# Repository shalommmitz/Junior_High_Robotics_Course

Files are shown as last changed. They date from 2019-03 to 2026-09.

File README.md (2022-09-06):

<p align="center">
  <h3 align="center">Junior High Robotics Course</h3>

  <p align="center">
    An open-source and open-hardware course, designed to make Technology cool.
  </p>
</p>
<br>

This repository holds the materials of a robotics course that was given for more than 10 years to gifted students. The course teaches the basics of electronics, programming and robotics. The course aims to make students 'at home' with advanced, deep technologies, in hope that more of them will choose STEM as careers.
During the course, the students build a robot, which is affordable enough so they can take it home at the end of the year. This is a great motivator.

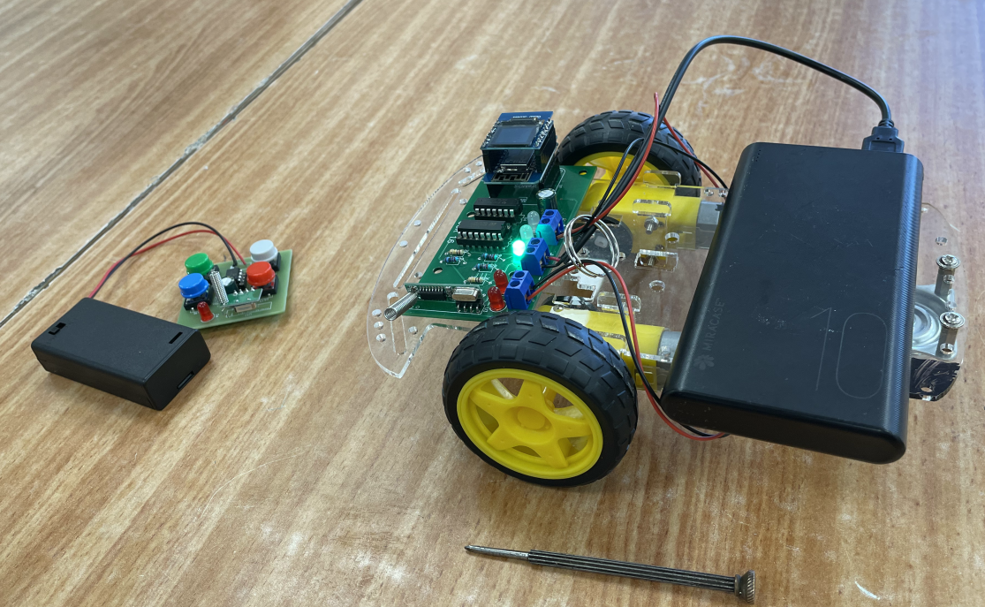
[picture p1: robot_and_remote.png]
The robot and remote-control assembled


## Table of contents

- [Course Overview](#course-overview)
- [Content of Subdirectories](#content-of-subdirectories)
- [Prerequisites and Installing](#prerequisites-and-installing)
- [Author](#author)
- [License](#license)

## Course Overview

The course was given multiple years to 7Th, 8Th and 9Th graders at the i[Ofek Gifted school](http://projects.jerusalemfoundation.org/education/education/ofek-school-for-gifted-children.aspx), located at Jerusalem, Israel.
This course teaches the following

- The basic principles of electricity (Ohm's law and related terms)
- The basic principles of electronics, including use of multi-meter
- Reading electronics schematics
- Design of PCBs
- Soldering and trouble-shooting electronic circuits
- Basic Python skills

## Content of Subdirectories

- documents_presentations:
    - [The course syllabus](documents_presentations/syllabus.md)
    - [The list of parts used in the course, including links for each item in Ali-Express](documents_presentations/22_08_Ofek_robotics_purchases.xlsx)
    - [Presentation: Motivation for the course (Hebrew)](documents_presentations/advocating_technology_at_junior_high_Hebrew.pptx)
    - [Presentation: Overview of Electronics (Hebrew)](documents_presentations/electronics_overview_Hebrew.ppt)
    - [Hands-on fun way to illustrate voltage/current/resistance and their relationship (Hebrew)](documents_presentations/ohm_law_experiment.doc)
    -[Presentation: Overview of the robot (Hebrew)](documents_presentations/robot_overview_Hebrew.ppt) 

- remoteControl_firmware
- remoteControl_hardware
- robot_firmware
- robot_hardware
- robot_PC_software

## So, you want to teach this course ?

Here is what you will need:

- One time: One item of: PIC programmer, [PIC basic pro compiler](http://store.melabs.com/prod/PBP/PBP3-2.html)
- One time: For each student: A PC or laptop,working bench, a soldering iron
- One time: For every 5 students: a multimeter, a magnifing glass, pliers, cutter 
- Every year: [kits, robots and remote parts](documents_presentations/22_08_Ofek_robotics_purchases.xlsx)

## Author

**Shalom Mitz** - [shalommmitz](https://github.com/shalommmitz)

## License

This project is licensed under the MIT License - see the [LICENSE](LICENSE ) file for details.

## Apendix A: Parts List
| Quantity per student | Quantity Ordered | Description | Order | Del | Price USD | Used by | URL | |
|---|---|---|---|-----|---|---|---|---|
| | | | | | | | | |
| First Project (Kit) | | Kits | | | | | | |
| 4 | 5 | Hour-glass leds kit | 24Aug | | 17.71 | Initial kit  | https://www.aliexpress.com/item/1005002305819829.html | |
| 4 | 5 | Alarm clock kit | 24Aug | | 26.59 | Initial kit  | https://www.aliexpress.com/item/4000302775578.html | |
| 4 | 5 | Metal detector | 24Aug | | 9.14 | Initial kit  | https://www.aliexpress.com/item/33004705384.html | |
| Parts for robot and remote | | | | | | | | |
| 15 | 8 | Wheel Chassis | 01Sep | | 68.92 | robot | https://www.aliexpress.com/item/1005004589986093.html | |
| 0 | 7 | Wheel Chassis | 04Sep | | 60.34 | robot | https://www.aliexpress.com/item/1005004589986093.html | |
| 1 | 0 | 25 PCB version 1.7 | 03Sep | | 27.51 | robot | https://jlcpcb.com/ | |
| 1 | | PCBs for Remote | | | | remote | https://jlcpcb.com/ | |
| 2 | 2 | 10 uP PIC12F675 I/P | 04Sep | | 26.7 | remote | https://www.aliexpress.com/item/4000052205464.html | |
| 1 | 0 | 1000 LED | | | | robot | https://www.aliexpress.com/item/Free-shipping-1000PCS-5-value-5mm-diffused-red-yellow-blue-green-white-R-G-B-W/2048531042.html | |
| 1 | | 100 x 40-pin stright Female | | | | robot | http://www.aliexpress.com/item/100PCS-2-54mm-40-Pin-Stright-Female-Single-Row-Pin-Header-Strip-PCB-Connector/32596334536.html | |
| 3 | 3 | 10 L239D DIP IC | 04Sep | | 7.1 | robot | https://www.aliexpress.com/item/32844099228.html | |
| 1 | 3 | 10 14pin DIP socket | 04Sep | | 7.02 | robot | https://www.aliexpress.com/item/32799921132.html | |
| 2 | 3 | 10 16pin socket | 04Sep | | 6.42 | robot | https://www.aliexpress.com/item/32800892159.html | |
| 15 | 15 | Wemos D1 Mini V3.0.0 | 05Sep | | 32.55 | robot | https://www.aliexpress.com/item/1005001621896145.html | |
| 12 | 15 | Oled Display 64x48 | 05Sep | | 27.75 | robot | https://www.aliexpress.com/item/1005001621659840.htmlhttps://www.aliexpress.co/item/Free-Shipping-0-66-inch-Wemos-Oled-64X48-IIC-I2C-LCD-OLED-LED-Dispaly-Shield-for/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 | |
| 2 | 2 | 20 8pin socket | 05Sep | | 4.02 | remote | https://www.aliexpress.com/item/32878848553.html | |
| 0 | 0 | 100 x 1000u cap | | | | remote+robot | http://www.aliexpress.com/item/Free-Shipping-DIP-Electrolytic-capacitor-1000UF-16V-8-12mm-100pcs-lot-NEW-in-stock-if-can/2010462041.html | |
| 5 | 0 | 500pcs 220 ohm resistors | | | 8.37 | remote+robot | https://www.aliexpress.com/item/32829082640.html | Note: 5 per robot, 1 per remote |
| 2 | 0 | 200pcs 100K ohm | | | 3.31 | robot | https://www.aliexpress.com/item/1005002000626397.html | Note: 2 per robot |
| 12 | 25 | RF TX RX + ANT | 05Sep | | 21.29 | remote+robot | https://www.aliexpress.com/item/32980820915.html | |
| 3 | 7 | 25pcs push btn | 05Sep | | 7.25 | for remote | https://www.aliexpress.com/item/32834276752.html | |
| 0 | 0 | 10 2 AA Battery Holder | | | 6.99 | for remote | http://www.aliexpress.com/item/10PCS-2-AA-3A-Battery-3V-Holder-Box-Case-with-5-5-Leads-and-ON-OFF/1985883563.html | |
| 1 | 2 | 20 pcs SN74HC04N IC | 05Sep | | 8.06 | for remote | https://www.aliexpress.com/item/1005002920656915.html | |
| 4 | 13 | 10 pcs terminal block | 05Sep | | 24.12 | remote+robot | https://www.aliexpress.com/item/4000899450689.html | |
| 12 | 7 | power bank | 05Sep | | 63.7 | for robot | https://www.aliexpress.com/item/1005004701731413.html | |
| | 7 | power bank | | | 63.7 | for robot | https://www.aliexpress.com/item/1005004701731413.html | |
| 12 | 6 | USB power cable | 05Sep | | 4.32 | robot | https://www.aliexpress.com/item/4001022946203.html | |
| | 6 | USB power cable | | | 5.32 | | https://www.aliexpress.com/item/4001022946203.html | |
| | 6 | USB power cable | | | 6.32 | | https://www.aliexpress.com/item/4001022946203.html | |
| | | TOTAL USD | | | 532.88 | | | |

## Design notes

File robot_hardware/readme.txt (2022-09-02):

The files in this folder describe the robot hardware.
You might use the free version of the software 'diptrace' to view or modify those files.
There are two versions of the schematics as .PNG: white (optimized for viewing) and black (optimized for printing)
The .zip file contains the production files, used to manufacture the PCBs.
I had good experience with jlcpcb.com.

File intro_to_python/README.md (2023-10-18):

## An introduction to Python

Lesson 1: 

  - Teach the 3 basic data types (num, string, bool), print. 
  - Exercise w/online-python.com: print values, print multiple values

Lesson 2: 

  - Teach list (the first non-basic data type)
  - Concept: subordinate lines
  - Teach loop
  - Exercise: print (unformatted) mult table

Lesson 3: 
     
  - Introduce replit.com. 
  - Demo: run `draw_a_point.py` in replit
  - Exercise: draw a line (using loop)

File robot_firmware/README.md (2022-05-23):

Shalom Mitz			17th May 2022

# OVERVIEW

The procedure below shows how to program the robot 'brain'.

The brain is the 'WEMOS D1 Mini' part, which is based on the ESP8266 processor.
The brain can be programmed with or without the display-module connected.

# Steps:

1. Install software:

   1.1. On Windows: 
       
        - Install Python: Download and install the latest version from https://python.org 
        
           IMPORTANT: Turn on "Add Python to Path" at first screen of installation
        - Install the drivers for the WeMOS serial drivers

   1.2. Install the sw to burn the 'robot brain' (=ESP8620):   `pip install esptool`
   1.3. Install the sw  that will transfer files to the robot brain: 'pip install adafruit-ampy`
   
2. Connect the robot-brain to a PC, using a normal 'Android' micro-USB cable

Note: 
   Normally we program the brain with the firmware-image file present in this directory.
   However, you can also use the generic microPython image, present at http://micropython.org/download#esp8266

3. Program the brain with the microPython image: 
   - ON LINUX: 

       Run './initial_firmware_loading_for_linux'

   - ON WINDOWS:

       Run 'initial_firmware_loading_for_windows'

4. Find the serial port used by the robot-brain:
  
   The easiest way is to look at the messages when running esptool (previous step).
   
   If this does not work:
  
   ON LINUX:
   
   Using terminal, run 'ls /dev/ttyUSB*'. This should show /dev/ttyUSB0
   If only /dev/ttyUSB2 exists, you should edit the file 'initial_firmware_loading_for_linux' to reflect this.
   If the 'ls' command above does not show anything, the D1 was not recognized.
   This must be resolved before continuing.

   ON WINDOWS:
   
      Normally, "COM4" is used on Windows
      To see the actual port:
         - Open the "Device Manager":
             - Right-click on "Computer" or "This PC" icon
             - At the menu that will open, choose "Manage"
             - choose "Device Manager"
         - Expand "LPT and COM ports"
         - Notice the existing serial ports (called "COM" and a digit)
         - Plug-in the robot brain to the PC, using a USB cable
         - Notice the name of the new COM port. This is normally "COM4"

5. Burn the additional files:
   Run:

     - On Windows: `send_all_files_windows.cmd`
     - On Linux:   `./send_all_files_linux`

   You can run the command "import verifyFiles" to verify that the files were correctly loaded.

6. Sanity check: disconnect the D1 from the USB and plug back.
   When you re-connect the D1, one of the LEDs should blink twice.
   If the LED does not blink, or blink all the time, try to run 'burn' again
   Note: Detailed instructions of programming the D1 and troubleshooting can be found at:
   http://docs.micropython.org/en/latest/esp8266/esp8266/tutorial/intro.html#deploying-the-firmware

# Testing:

1. Connect to the brain: 
   Once connected, the brain looks like serial port at /dev/ttyUSB0 (rarely: /dev/ttyUSB1) on Linux or CAM4 on Windows.

   You can connect to it using: putty, minicom, screen, or any other 'terminal emulation' software
   Here are detailed instructions using Putty:

   - Open putty
   - Define a serial session: 
      - Choose "Serial" as the connection type     
      - Set the port (Normally: COM4 or /dev/ttyUSB0)
      - Set the speed: 115200
   - Open the connection: Click on "Open"
   - Press "Enter": you should see the Python prompt (>>>)
     Do not continue to the next steps before you get the prompt !
     You can try to close Putty, disconnect the brain, reconnect the brain and launch putty again.
     You can also try to burn the image again.

   Once you are connected, hit "Enter" few times, and you should get the ">>>" REPL prompt.
   If you do not get the prompt, try unplug/plugin from USB. If this fails, try 'burn' again.
   There is no point to continue w/o the REPL prompt.

   Also, once you are connected, you can type the command "import demo".
   This should send few strings to the console and then display some pictures on the attached display. 

Steps that are repeated each time the D1 is used:

1. Connect to the PC/laptop to the WiFi access-point created by the D1:

   Look at the available WiFi networks for a network called "MicroPython-xxxxxx" (the 'xxxxxx' part is different for each D1)
   Connect to this network.
   Note: This will probably disconnect you from the Internet. 

2. Connect to the robot using WebREPL:

   If needed, download the webrepl files from  https://github.com/micropython/webrepl.
   Open the file "open webrepl.html in a browser. 
   You should get a prompt to choose password (first time) or login.
   After login, you should get the ">>>" prompt. You are also able to upload and download files.
   There are more details at: https://github.com/micropython/webrepl

3.  Using WebREPL, import the 'robot' module:
    
    Once you get the ">>>" prompt,  enter the command `import robot`
    This will define 4 outputs:
    pwmRight, dirRight, pwmLeft, dirLeft
    Each of those can be set to high or low, for example:
    pwmRight.low() or pwmLeft.high() 
    Experiment: those 4 pins control the motors.

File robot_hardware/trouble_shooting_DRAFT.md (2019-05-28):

My robot does not move
----------------------
Those are the possible causes:

1. No power
2. 'Brain' not fully functional
3. Motors not connected
4. Issue with the H-Bridge IC (U2, L293D)

Procedure to Fix:

1. Verify that power is Ok
   The center LED should be on. If not, you have no power.
   If the LED is on, use multimeter (at V-DC-20V position) to measuer the input voltage. It should be atleast 4.8V. If less, you probably have to change the battries.
   If there is no voltage, start measuring voltage from the battries, until you find where is the disconnect.

2. Verify brain works Ok
   We proceed to this state assuming we verified that power is Ok.
   The easiest way to verify that the brain is fully functional is to switch termorarirly to brain from a known-to-be-working robot. If another, known-to-work, brain is not available, the best way is to continue the procedure, while watching carfully the performance of the brain. Another possiblity is to reflash the brain (rarly needed) and reload all the files.

NEED TO ADD LINK TO FLASHING THE FILES

3.  Verify that the motors are connected
   This one is easy: Using your hand, turn one wheel both ways. One of the two LEDs associated with each whell should light momentarily. Repeate for the other wheel. Fix any issue found.

4. Verify the correct operation of the H-bridge.  
   Issues with the H-bridge are the most common reason why robot won't move.
   Here are the steps to debug this IC:
   4.1. Open the schematics and zoom on U2. The schematic is at NEED TO ADD LINK TO SCHEMA
   4.2  Get a multimeter, and set it to measure Volts-DC-20V. Connect the "-"/black probe to one of the ground point of the robot, for example at the battries "-" terminal.
   4.3 Look at the schema. The H-bridge IC has two connections to the power-supply. Check that both of those connections are connected to the 5V or so comming from the battries.
   4.4 Verify connection from the brain to the pwmLeft and pwmRight points
       NEED TO ADD CODE
       NEED  TO ADD LINK TO PROCEDURE TO GET REPL (Python prompt).

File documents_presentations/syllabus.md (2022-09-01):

# Syllabus

## Background

This course evolved during the 11 years I have been teaching at the Ofek school for gifted children, in Jerusalem Israel.

It is composed of two courses: Basic course and Advanced course.
Both courses are for a full academic year, once weekly, each session is two academic hours.
In a typical year, this means 26 sessions.

The kids are mostly 7th or 8th grades.

## Curriculum Highlights for basic course

1. Basic theory and practice of electronics
   In parallel: build a small kit: mainly to put the theory in context and to practice soldering
2. Design the PCB for the remote control
3. Start building the robot
4. Build the remote control
5. Finish building the robot
6. Test/troubleshoot
7. If time allows: Study a bit of Python and program the robot

## Curriculum Highlights for the advanced course

1. Review/study Python
2. Make sure robot work, fix as needed
3. Lake: a fun exercise to develop Python skills
4. Basic machine vision
5. Controlling the robot using Python
6. Tie everything together: Use machine vision to control the robot
7. As time allows: basic neural network in Python

## Detailed Basic Course Syllabus

Note: The numbers are the week

 1. Teach: Electricity basic theory: 
    - Ohm law, resistors, basic circuit calculations
    - Review: electrical charge, current, voltage (charge=current*time)
    - Fun optional project: take bottles, fill w/water, simulate resistance

        - Prepare corks w/one, two or three holes
        - Mark 3 levels on the bottles
        - Ask kids to measure water drip out of the bottles (into one-time cups) on each cork/water level permutation
        - Ask them to draw the relationship and deduct Ohm's law

  2. Teach: Electronics hands-on basics: 

        - Use of multi-meter
        - Soldering: How-to + Review safety points: danger of fire, damage to eyes, burns, mark tables
        - Identifying components

     Hands-on:

        - Solder wire (each 5 cm or so) into shapes, such as rectangular or triangle

  3-5. Hands-on: First build project: Various kits
       Present to the kids examples of electronic-schematics
       Some effort to debug the kits - not insist on all kits working

  6-8. Teach:

       - Basics of Radio-frequency: what is RF, Uses to send data, modulation, Antenna
       - PCB: Alternatives (wires, wire-wrap), what it is, one side/two sides/multiple layers
       - Remote control basic-principles and schematics
       - Show installation and basic usage of DipTrace sw

       Hands-on:
       - Draw schematics for the remote using diptrace
       - design PCB for RF remote using diptrace

  10. Teach:

      - Presentation: the robot components
      - Integrated Circuits: Tube to Transistor to IC. Examples uses + packages

      Hands-on: build robot chassis, tests w/just motors and batteries

  11. Teach: Robot schematics
      Hands-on: continue build chassis
  12-15. Hands-on: Build Robot main board
  16. Hands-on: Debug robot
  17-18. Build remote control (dependant on PCB arriving)

  If time allows:

    - Fun: robot competitions, using the remotes
    - Control the robot from phone or PC using WiFi
    - Customize the picture displayed by the robot-display

A Real Basic Course (partial Corona - atypical):

 - Lesson #1 (12Oct2021): Basic soldering
 - Lesson #2 (19Oct2021): ?
 - Lesson #3 (16Nov2021): Assembling robots
 - Lesson #4 (23Nov2021): Assembling robots
 - Lesson #5 (07Dec2021): Finishing of robot chassis assembly + into to designing the remote PCB
 - Lesson #6 (14Dec2021): Remote PCB intro and start design
 - Lesson #7 (21Dec2021): Continue remote-control PCB design
 - Lesson #8 (28Dec2021): Continue design the remote PCB
 - Lesson #9 (04Jan2022): Finish remote PCB design and introduce robot schematic
 - Lesson #10 (11Jan2021): Finish previous tasks + explain robot schematics + start build rob
 - Lesson #11 (18Jan2021): Review robot schematics, tube-->transistor-->IC, cont build robot elect
 - Lesson #12 (01Feb2021): Review robot schematics + assemble robot pcb
 - Lesson #13 (08Feb2021): Hands-on intro to Python (vars, for, if)
 - Lesson #14 (22Feb2021): Build the remote control
 - Lesson #15 (22Mar2021): Continue assembling the remote control PCB
 - Lesson #16 (29Mar2021): Continue remote-control assembly
 - Lesson #17 (05Apr2021): Remote: assemble PCB + test + burn uPs
 - Lesson #18 (26Apr2021): Continue remote-assembly: continue burn chips
 - Lesson #19 (03May2021): Burn firmware to robot
 - Lesson #20 (10May2021): Burn sw to the robot brain

## Advanced Course (Work in Progress):

   1-3. Study Python:
        Either frontal intro w/exercises OR self study at CodeAcademy

   4. Teach: intro to network protocols, bits, bytes, hex. The robot protocol

      Exercise: Divide class to groups and challenge them to decode and parse messages:
          The messages will contain specs for food to server at restaurant
          One group will create the messages and the other group will draw the 'plates'
          
          Decrypt the "lake" protocol ???
          
   5. Personal project

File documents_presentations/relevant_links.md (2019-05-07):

How to read schematics: https://learn.sparkfun.com/tutorials/how-to-read-a-schematic

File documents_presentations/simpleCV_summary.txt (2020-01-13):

from SimpleCV import *

# create image object by reading file
img = Image("old/donkey.jpg")

#show image object and wait for user to press ENTER
img.show()
raw_input(">")

#save image
#img.save("fn")

#clone the imgage
clone = img.copy()

#create smaller copy of the image
thumb = img.scale(90,90)

#cut part of the image
cropped = img.crop(100, 100, 50, 50)

#find corners
corners = img.findCorners()

#find blobs of color
blobs = img.findBlobs()
print blobs
blobs.draw()
img.show()
raw_input(">")
##blobs are returned in order of area, smallest first
#print "largest green blob at " + str(green_blobs[-1].x) + ", " + str( green_blobs[-1].y)

bigface = face.scale(3)

rotated = lenna.rotate(90)

#split image into channels and unite again
(r,g,b)=img.splitChannels()
#new = img.mergeChannels(None,b,g)
new = img.mergeChannels(r,b,g)

#convert image to grey
img.toGray()

matrix = grey.getNumpy()
print matrix[0][0]

yellow_car = car.colorDistance(Color.YELLOW)
only_car = car - yellow_car
only_car.meanColor()
source.findTemplate(template,threshold=t,method=m)

img1.sideBySide(img2).show() #show sidebyside

img.dl().circle((10,10), 10, Color.RED) #draw circle

#get blobs
screensize = img.width * img.height
min_blob_size = 0.10 * screensize # the minimum blob is at least 10% of screen
max_blob_size = 0.80 * screensize # the maximum blob is at most 80% of screen
blobs = img.findBlobs(minsize=min_blob_size, maxsize=max_blob_size) # get the largest blob on the screen

#get width and height of image
    width = img.width;  height = img.height

#get distance from specified RGP color
imgDiffFromBlue = img.colorDistance( (21, 28, 63) )   #R, G, B

#Find edges of image
img = img.edges()

# find lines in image
lines = img.findLines()
#find longest line
longest_line = lines.sortLength()[0]

#find match of small pic in big pic
t = 5
#methods = ["SQR_DIFF","SQR_DIFF_NORM","CCOEFF","CCOEFF_NORM","CCORR","CCORR_NORM"] # the various types of template matching
m = "CCOEFF"
result = source
dl = DrawingLayer((source.width,source.height))
fs = source.findTemplate(template,threshold=t,method=m)
for match in fs:
    if match.y<38: continue #upper end of the pics is legit logos, matches not relevant
    dl.rectangle((match.x,match.y),(match.width(),match.height()),color=Color.RED)

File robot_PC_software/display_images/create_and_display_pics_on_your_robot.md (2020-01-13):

#How to create an image and display it on the robot's display

## Prerequisits:

Make sure all needed software is installed on your PC, as detailed at the files "install_needed_software_linux.txt" and "install_needed_software_windows.txt"
      During the installation, enable the check-box "Add Python 3.7 to Path"

Make sure the firmware and related files are loaded into the robot-brain. 
This is needed to be done only once on a new robot-brain.
The needed procedure is detailed at the folder 'robot_firmware'
  
## Create a new image that have the following attributes:

     size:  64 x 48   (This is the size of the display)
	 Color depth: black & white
   Or, you can start with one of the pre-existing images (.bmp) in this directory.
 
## Edit the image

You can edit the image with any image editing tool, such as mspaint, gimp, paint.net or pinta.

## Save the image, specifing the 'bitmap' format.

   It is important to keep the correct size and color depth

## Create the .hexImage file:

   The .hexImage file can be used by the robot software.
   
   Run:
   
        python convert_bmp_to_hex_Image.py <file_name.bmp>
        
   This will create a .hexImage file

## Preview the .hexImage file:

   run: 
   
        python show_hexImage_on_pc.py <file_name.hexImage>.

   If you don't like what you see, you can edit/save/convert/preview until happy :-)

## Upload the .hexImage file to the robot:

   -  Find which COM port the robot-brain is using:
      ON LINUX: the name is normally /dev/ttyUSB0 (or sometimes /dev/ttyUSB1)
      ON WINDOWS:
      Open the "Device Manager":
         - Right-click on "Computer"
         - choose "Manage"
         - Expand "LPT and COM ports"
         - Notice the existing serial ports (called "COM" and a digit)
         - Plug-in the robot brain to the PC, using USB cable
         - Notice the name the new COM port. This is normally "COM4"

   Loading the file might be done using ampy or webrepl

   Using ampy:   
   
       Linx:  ampy -p /dev/ttyUSB0 put <file name>
   
       Windws:  ampy -p com4 put <file name>
   
   Details on ampy: https://learn.adafruit.com/micropython-basics-load-files-and-run-code/install-ampy
   
   Details on webrepl: https://github.com/micropython/webrepl

## Displaying the image on the robot:

Connect to the robot and get the REPL prompt.  
Connecting to the robot can be done:

- Using WiFi: 

    Download from github the repository "webrepl.
    
    The robot 'publish' a WiFi network, called 'born' by default.
    Connect to this network.

    Now, open the .html page in the 'webrepl' repository, by double-clicking on the file.

- OR, using a USB cable:

    Connect the robot to a PC using a standard 'Android' usb cable
    Run any 'serial terminal' program, such as putty or minicom.

    On Windows, use Putty: 
      - Select "serial" as the connection type
      - Open the Serial-ports parameters window: At the left-side "Category" tree, choose the bottom entry, which is "Serial"
      - Set "COM4" as the port
      - Set "115200" as the speed.
      - Choose "Flow control" to "None"

    On Linux, use minicom:
    - Disable hardware-flow-control
    - use "/dev/ttyUSB0" as the port 
    - Specify "115200" as the speed.

    When you are correctly connected to the robot, you should get the ">>>" prompt.
    You might need to press the "Reset" button

- Displaying the image
    Run the following:
   
       >>> import display_hexImage as d
       >>> d.display_image("abc.hexImage")

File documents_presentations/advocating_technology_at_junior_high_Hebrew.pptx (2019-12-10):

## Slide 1

שיווק הי-טק בחטיבה

שלום מיץ מאי 2019

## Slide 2

תוכנית

- התנסות
- מי אני
- למה
- עשיה
- יתרונות
- חסרונות
- התנסות

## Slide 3

התנסות

- לימוד בינרי והקס
- או סרט של רובטים רוקדים ?

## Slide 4

מי אני

- מהנדס אלקטרוניקה ומחשבים
- Technical Leader at Cisco Now at Synamedia
- מלמד פעם בשבוע ב 11 השנים האחרונות
- מורעל טכנולוגיה ומחשבים

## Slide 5

למה

- להרעיל את התלמידים לטכנולוגיה
- חשיפה לאיך הי-טק עובד
  - טעימה של איך פיתוח טכנולוגיה עובד
- נצחונות בהתמודדות אם אתגרים אמיתים
- הטפה לרעיונות ה- Open Source כולל הטפה ל- Linux
- לקרב בנות ל- STEM

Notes: What is unique/interesting in Hi-tech:
Answers not known ahead of time
Agenda not well defined - “somehow” reach goal
No authoritative source of knowladge
Up=to-date technology used
Course changes every year
Real-world tools used
Everything done for the first time (sort of)
Lot and lots of English...

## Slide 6

עשיה

- שעה וחצי, פעם בשבוע, כיתות ז עד י
- קורס בסיסי: אלקטרוניקה ובנית רובוט
- קורס מתקדם: תכנות הרובוט וראית מכונה
- סביבה “חצי אפויה” -- כמו בחיים
- בסוף הקורס: רובוט לקחת הביתה
- חומרי הקורס ב- github
- junior_high_robotics_course

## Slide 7

עשיה: השיעור

- מבנה השיעור:
  - 10%: הצגת המטרה והסבר קצר
  - 90%: עבודה עצמית – המורה כ- enabler
- שימוש בכלים “מהעולם האמיתי”
- עידוד פרויקטים עצמיים
- המורה לא כל יודע
- עידוד עזרה הדדית, ואחריות

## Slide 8

יתרונות

- התלמידים נהנים
- המורה נהנה
- יותר תלמידים ילמדו ויעבדו בהי-טק ???
- אורינות טכנולוגית משופרת ?
- קרוב בנות ל- STEM ?
- לימוד וחקר כהנאה - חוויה מתקנת ?
- מקום לשונות

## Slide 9

חסרונות

- לא כולם מבינים (כולל המורה)
  - כמו בעולם האמיתי
- מעבר על פני השטח
- לא כולם מצליחים
- דורשני ולא סלחני לחיסורים

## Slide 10

סוף והתחלה

- התלמידים מסתכלים על הדפסות התוכנה של הרובוט
- תלמיד א: איך מתי מתאים שאשתלט על המחשב שלך ונפעיל את המצלמה ? לשנות את זה ?
- תלמיד ב: אני לא יודע. בא נסתכל על הקוד.

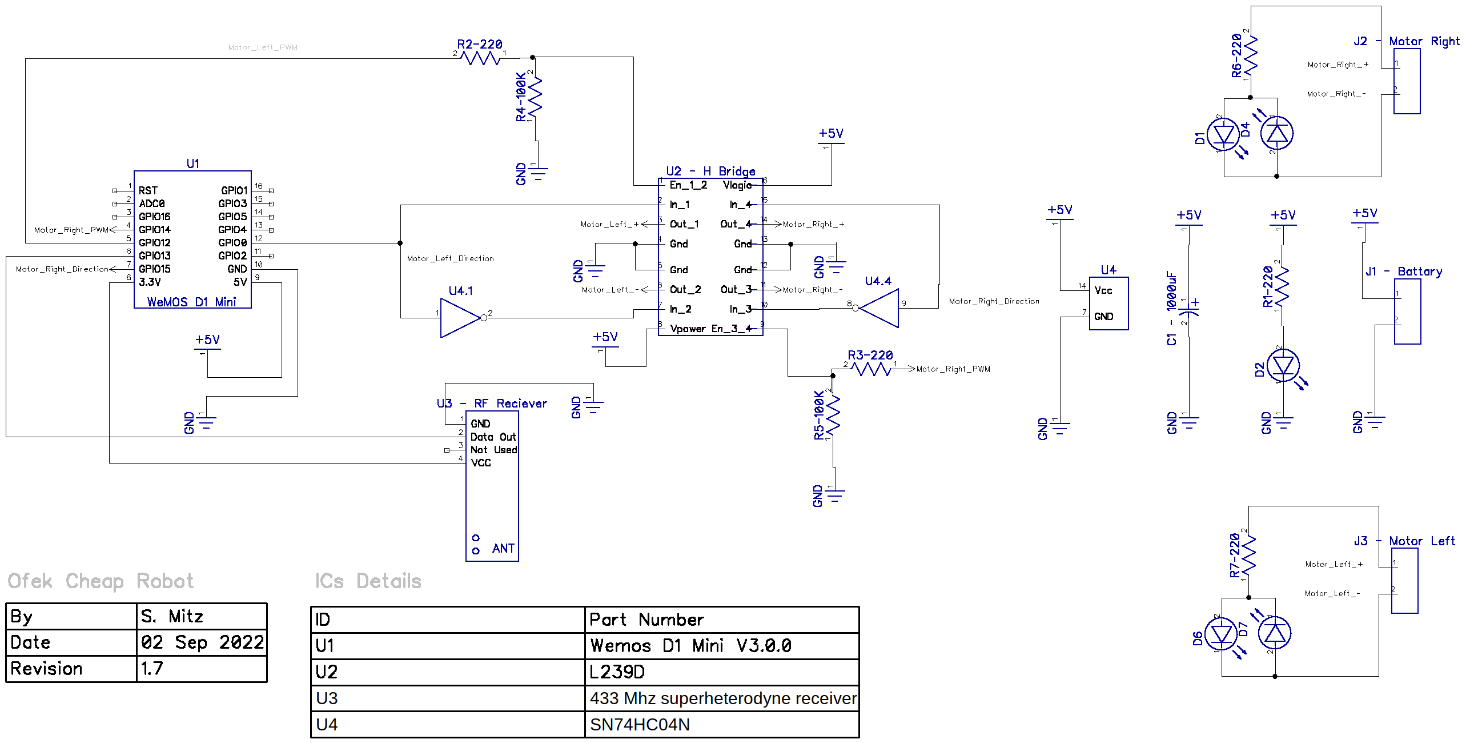
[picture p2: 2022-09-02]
robot_hardware/robot_v17_scematics_white.png

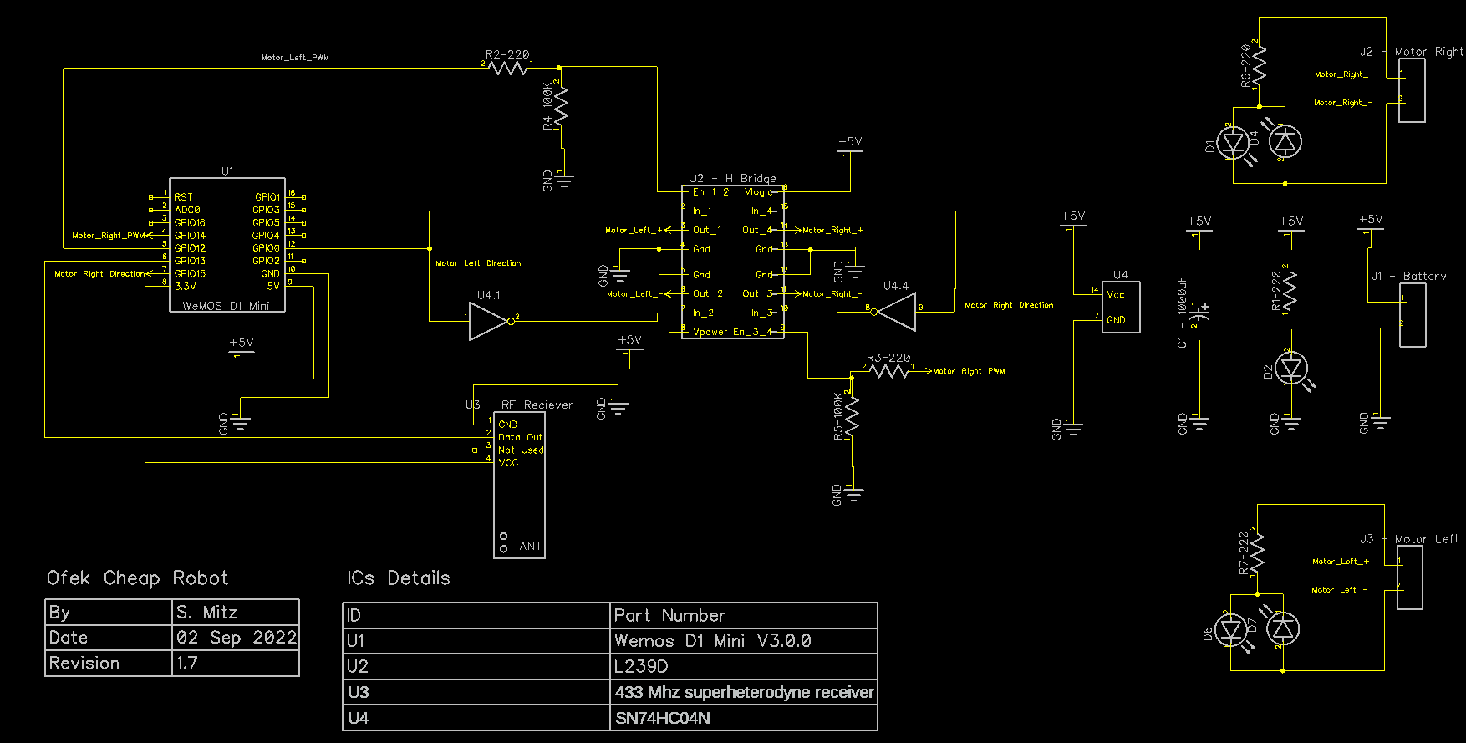
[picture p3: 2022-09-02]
robot_hardware/robot_v17_scematics_black.png

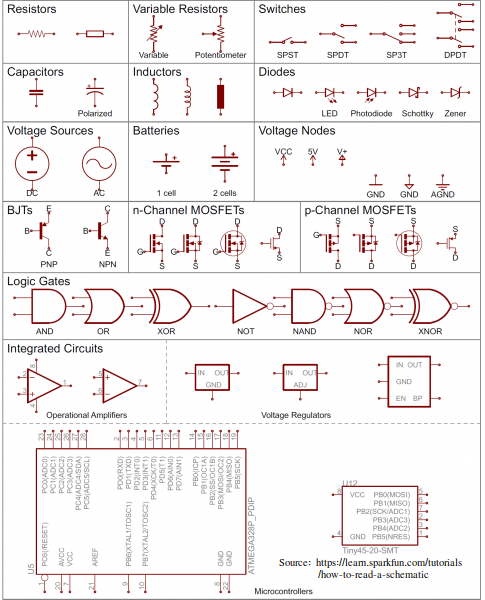
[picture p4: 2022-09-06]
documents_presentations/symbols_in_schematic.png

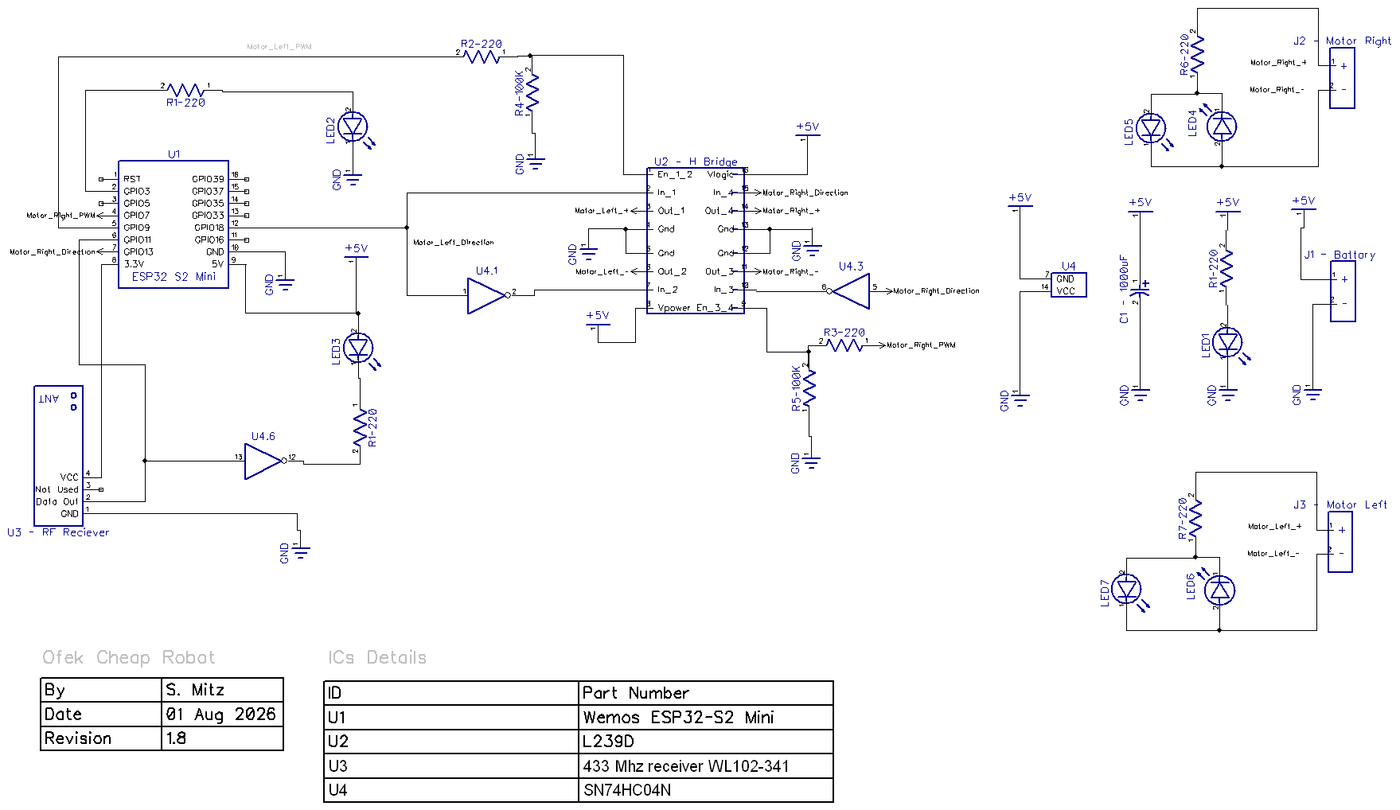
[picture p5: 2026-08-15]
robot_hardware/robot_schematics_v18_image.png

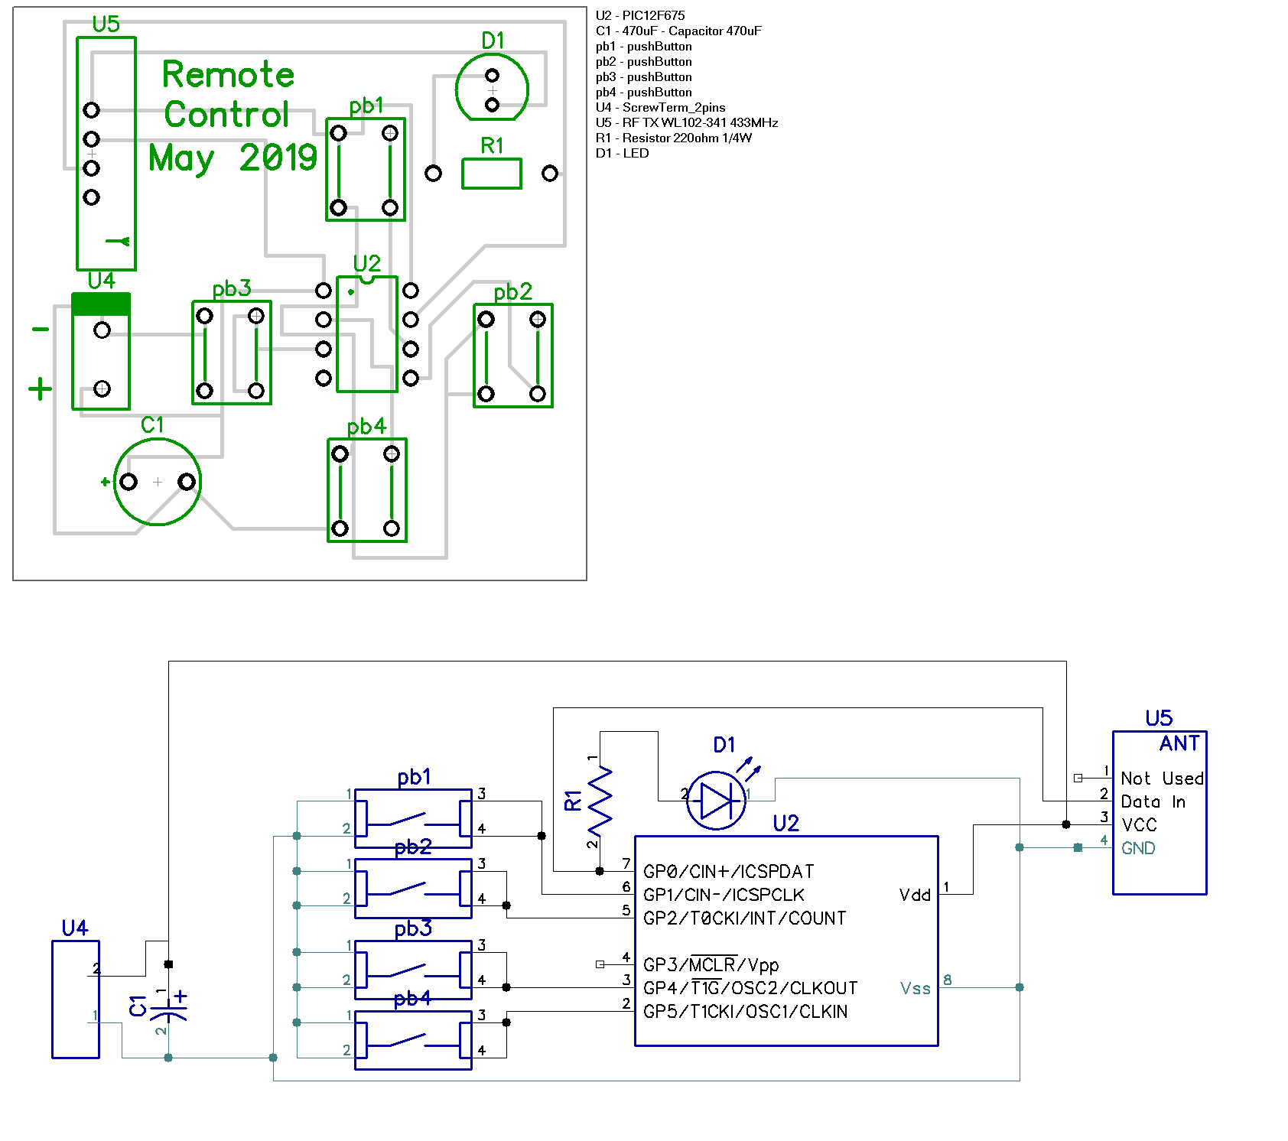
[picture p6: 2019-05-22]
remoteControl_hardware/remote_PCB_scheme.png

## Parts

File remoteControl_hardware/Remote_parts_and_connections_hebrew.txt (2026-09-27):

שלום מיץ                                  אוקטובר 2025

הרכיבים שבשימוש בשלט המרוחק ואיך לחבר אותם
===========================================

מסוף
שם באנגלית: Terminal או Screw Terminal
תפקיד: נקודות חיבור לשני הכבלים המגיעים ממחזיק הבטרייה ל- PCB
חיבור: רגל 1 ל 3V     רגל 2 לאדמה
הערה: ה + של הבטרייה נקרא לפעמים Vdd או Vcc או 3V. ה - של הבטרייה נקרא Ground (GND) או Vss.

קבל
שם באנגלית: Capacitor
תפקיד: מייצב את המתח: מספק דרישה לזרם הרבה יותר מהר מהבטריה
חיבור: הרגל המסומנת ב + ל- 3V והרגל השניה לאדמה

מעבד או מעגל משולב
שם באנגלית: Microprocessor או System on Chip
תפקיד: מריץ את התוכנה ששולחת פקודות לרובוט ע"י שידורי רדיו.
חיבור:
		- רגל מספר 1 מתחברת ל Vcc ורגל מספר 8 לקרקע
		- רגליים מספר 2,3,5 ו-6 מתחברות למפסקים; הן משמשות כקלט
		- רגל 7 מתחברת למשדר רדיו (ל Data-in) ולנגד-דפ"א
		- אין שימוש ברגל 4	
הערה: המעבד לא מולחם ישירות ל PCB אלא לתושבת (התושבת מולחמת ל PCB)
		  זה לא משנה את המעגל המודפס (PCB) או את הסכמה.

נגד
שם באנגלית: Resistor
תפקיד: מגביל את הזרם שעובר בדפ"א
חיבור: רגל אחת לפין 7 של המעבד ורגל שניה לפלוס של הדפ"א

דפ"א (דיודה פולטת אור)
שם באנגלית: LED: Light Emiting Diode
תפקיד: מאירה כשהמעבד משדר
חיבור: הרגל הפלוס לנגד ורגל המינוס לאדמה

מעגל שידורי הרדיו
שם באנגלית: RF Tx Module (Radio Frequency Transmit Module)
תפקיד: משדר פקודות מהמעבד-הזעיר לרובוט כגלי רדיו
חיבור:
		- רגל Vcc ל 3V
		- רגל GND לאדמה
		- רגל Data-in לרגל 7 של המעבד
		- אין שימוש ברגל not used
	הערה: צריך להלחים אנטנה למעגל שידורי הרדיו. זה לא משפיע על המעגל המודפס.
	
מפסקים
	יש 4 מפסקים, כל אחד מבחבר לרגל אחרת של המעבד
	שם באנגלית: Push Button
	תפקיד: כשלחוץ, מאותת למעכד לשלוח פקודה
	חובורים:
	 - המפסק הראשון: צד אחד לאדמה (שני המגעים) וצד שני לרגל 2 של המעבד
	 - המפסק השני: צד אחד לאדמה (שני המגעים) וצד שני לרגל 3 של המעבד
   - המפסק השלישי: צד אחד לאדמה (שני המגעים) וצד שני לרגל 5 של המעבד
   - המפסק הרביעי: צד אחד לאדמה (שני המגעים) וצד שני לרגל 6 של המעבד

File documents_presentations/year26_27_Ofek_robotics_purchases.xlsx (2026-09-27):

Description | Order Date | Delivery Date | Cost | Used by | URL
Kits
ESP32 CAM |  |  |  | Adv course | https://www.aliexpress.com/item/1005006028862997.html
Hour-glass leds kit |  |  |  | Initial kit | https://www.aliexpress.com/item/1005002305819829.html
Alarm clock kit |  |  |  | Initial kit | https://www.aliexpress.com/item/4000302775578.html
spinner |  |  |  | Initial kit | https://www.aliexpress.com/item/1005007011389049.html
sp bat (cr927) |  |  |  | Initial kit | https://www.aliexpress.com/item/1005006077844872.html
10 x Rotary |  |  |  | Initial kit | https://www.aliexpress.com/item/1005003136551260.html
5 x bug kit yellow | 11Aug | 23Aug | 12.15 | Initial kit | https://www.aliexpress.com/item/1005003136551260.html
10 x bug kit Gold | 11Aug | 23Aug | 15.59 | Initial kit | https://he.aliexpress.com/item/1005001763427614.html
20 bug bat (cr2032) | 23Aug | 07Sep | 11.52 |  | https://he.aliexpress.com/item/1005007897844145.html
10 x clock | 11Aug | 23Aug | 23.72 | Initial kit | https://he.aliexpress.com/item/1005007328195814.html
LED circle |  |  |  | Initial kit | https://www.aliexpress.com/item/1005003755054439.html
Label printer | 19Aug | 24Aug | 59.91 |  | https://he.aliexpress.com/item/1005004557811934.html
10 x Wheel Chassis | 19Aug | 3Sep | 69 | robot | https://www.aliexpress.com/ssr/300000512/BundleDeals2https://www.aliexpress.com/ssr/300000512/BundleDeals2
5 x Wheel Chassis |  |  |  | robot | https://www.aliexpress.com/item/1005009534679971.html
25 PCB version 1.8 | 11Aug | 23Aug | 51.67 | robot | https://jlcpcb.com/
Solder wire 500G | 11Aug | 23Aug | 40.12 |  | https://he.aliexpress.com/item/1005008216404014.html
PCBs for Remote |  |  |  | remote | https://jlcpcb.com/
10 x 3 uP PIC12F675 I/P | 19Aug | 30Aug | 22.02 | remote | https://he.aliexpress.com/item/1005012707435934.html
3 x 240 LED (5mm) | 19Aug | 3Sep | 15.84 | robot | https://he.aliexpress.com/item/1005006015810729.html
100 x 40-pin stright Female |  |  |  | robot | http://www.aliexpress.com/item/100PCS-2-54mm-40-Pin-Stright-Female-Single-Row-Pin-Header-Strip-PCB-Connector/32596334536.html
4 x 10 L239D DIP IC | 19Aug | 30Aug | 13.56 | robot | https://he.aliexpress.com/item/1005006967713718.html
3 x 10 14pin DIP socket | 19Aug | 3Sep | 4.17 | robot | https://www.aliexpress.com/item/1005006130784050.html
5 x 10 16pin socket | 19Aug | 3Sep | 14 | robot | https://he.aliexpress.com/item/1005007238798198.html
10 x ESP32 S2 mini | 20Aug | 30Aug | 25.23 | robot | https://he.aliexpress.com/item/1005007684075877.html
10 x ESP32 S2 mini | 20Aug | 30Aug | 29.56 | robot | https://he.aliexpress.com/item/1005006828096971.htm
5 x 4 0.66” OLED display | 20Aug | 30Aug | 30.97 | robot | https://he.aliexpress.com/item/1005012135750580.html
4 x 20 8pin socket | 20Aug | 30Aug | 5.6 | remote | https://he.aliexpress.com/item/1005002452722959.html
2 x 40 x 1000u cap | 21Aug | 14Sep | 7.44 | remote+robot | https://he.aliexpress.com/item/32830074978.html
1000 220 ohm resistors | 21Aug | 31Aug | 6.86 | remote+robot | https://he.aliexpress.com/item/1005006802647239.html
1000 100K ohm resistors | 21Aug | 30Aug | 6.86 | robot | https://he.aliexpress.com/item/1005006802647239.html
20 RF TX RX + ANT | 21Aug | 31Aug | 27.52 | remote+robot | https://www.aliexpress.com/item/1005006365954443.html
3 x 25 pcs push btn | 21Aug | 30Aug | 5.78 | remote | https://www.aliexpress.com/item/32834276752.html | Note: 5 per robot, 1 per remote
12 2 AA Battery Holder | 21Aug | 30Aug | 12.96 | remote | https://he.aliexpress.com/item/1005005475607732.html | Note: 2 per robot
50 pcs SN74HC04N IC | 21Aug | 31Aug | 23.7 | robot | https://he.aliexpress.com/item/1005012836529502.html
4 x 20pcs PCB-to-wire | 16Aug | 3Sep | 22.35 | robot+remote | https://he.aliexpress.com/item/1005012098795616.html
3 x 10pcs 16850 charger | 17Aug | 3Sep | 4.17 | robot | https://www.aliexpress.com/ssr/300000512/BundleDeals2
2x10pcs bat chrger/boostr | 24Sep |  | 10.78 | robot | https://www.aliexpress.com/ssr/300000512/BundleDeals2?productIds=1005009393760108%3A12000048962658234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
240pcs duel side glue | 24Sep |  | 2.59 | robot | https://www.aliexpress.com/ssr/300000512/BundleDeals2?productIds=1005009393760108%3A12000048962658234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
3 x 10Pcs 18650 B Holder | 17Aug | 3Sep | 5.97 | robot | https://www.aliexpress.com/ssr/300000512/BundleDeals2
100pcs 10cm 20awd wir bl | 17Aug | 3Sep | 7.67 | robot | https://he.aliexpress.com/item/1005006995764528.html
100pcs 10cm 20awd wir rd | 17Aug | 3Sep | 7.67 | robot | https://he.aliexpress.com/item/1005006995764528.html
20m 22AWG wire blue | 17Aug |  | 6.61 | robot | https://he.aliexpress.com/item/1005004336218242.html
2 x 8 18650 battery | 22Aug | 06Sep | 35.65 | robot | https://he.aliexpress.com/item/1005008601127340.html
11 USB-C to wire 0.25 | 22Aug | 06Sep | 10.35 | robot | https://he.aliexpress.com/item/1005008773547453.html
7 USB-C to wire 0.25 | 22Aug | 06Sep | 8.09 | robot | https://he.aliexpress.com/item/1005008243389421.html
20 USB-C to A 05m | 22Aug | 06Sep | 17.59 | robot | https://he.aliexpress.com/item/1005008137418397.html
100x 8pin socket | 25Sep |  | 10.88 | robot | https://he.aliexpress.com/item/32674767032.html
100x 8pin stackable | 27Sep |  | 12.11 | robot | https://he.aliexpress.com/item/4000979967513.html
Soldering mat |  |  |  | lab | https://he.aliexpress.com/item/32863473926.html
2 x 3v motor |  |  |  | exper | https://he.aliexpress.com/item/1005008344939451.html
6xSoldering head |  |  |  | lab | https://aliexpress.com/item/1005008727145461.html
2xQuadCopter |  |  |  | Adv course | https://he.aliexpress.com/item/1005010124580055.html
 |  | Total: | 698.23

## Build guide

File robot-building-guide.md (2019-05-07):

#Building the Robot</h3>

Step by Step instructions for building the robot.

## Overview

- [Get the Hardware](#get-the-hardware)
- [Build the chassis](#build-the-chassis)
- [Build the Electronics](#build-the-electronics)
- [Setup a PC](#setup-a-pc)
- [Program the robot brain](#program-the-robot-brain)
- [Connect everything together](#connect-everything-together)
- [Test](#test)
- [Next steps](#next-steps)

## Get the Hardware

TBD

## Build the Chassis

   The chassis is the platform to which the rest of the parts are connected.
   The attached parts are: the battery holder, the motors, the wheels and the power switch.
   Build the chassis according to the instructions included in the chassis kit.
   When done, you should have the two motors and the battery holder attached to the chassis.
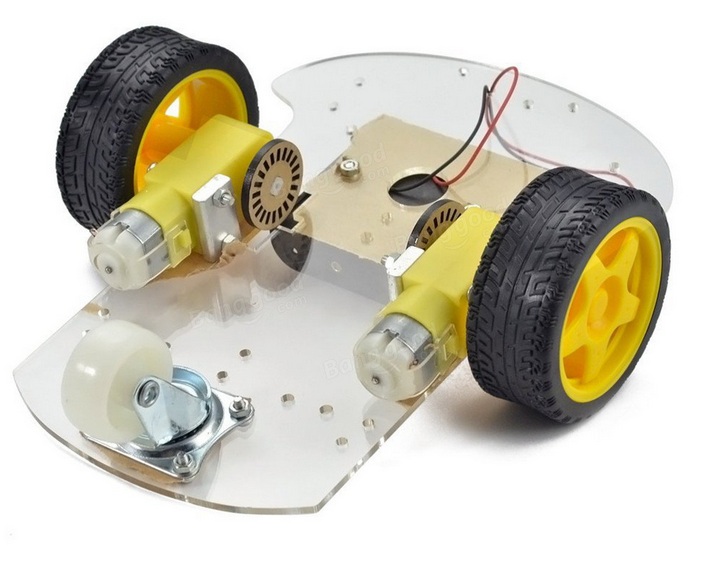
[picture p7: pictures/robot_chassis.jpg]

The assembled robot chassis.
Note: the battery-holder wires should be routed to the top, and not as shown.

## Build the Electronics:

### Solder the robot 'brain' and the associated display:

It is critical that all those parts are soldered exactly perpendicular.
    - the female 'socket' that connect the brain to the PCB
    - the male/female socket that is soldered to the brain
    - The 'male' pins that are soldered to the display.

The "brain" is the Wemos D1 Mini.

### Build the electronic board

Here you need to solder the parts detailed at "Robot_hardware" to the supplied PCB.

### The integrated circuits used:

- U1 is "Hex inverters" SN74LS04.
- U2 is "Bridge Power Driver" L239D
 
Tip: Start with parts at the center of the PCB, which are not high (because high parts make access to other parts hard).

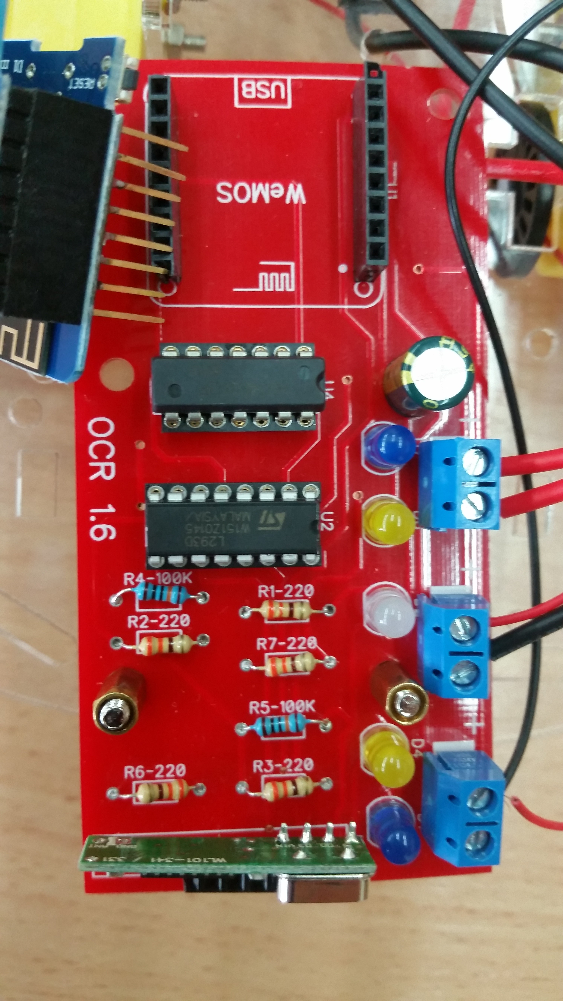
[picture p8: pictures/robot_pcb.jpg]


The assembled PCB.

Note: The RF-receiver at the very bottom is optional.

## Setup a PC

TBD

## Program the robot brain

TBD

## Connect everything together:

   Mount the PCB on the chassis. Connect the wires from the motors to the PCB. Connect the wires from the battery holder to the PCB.

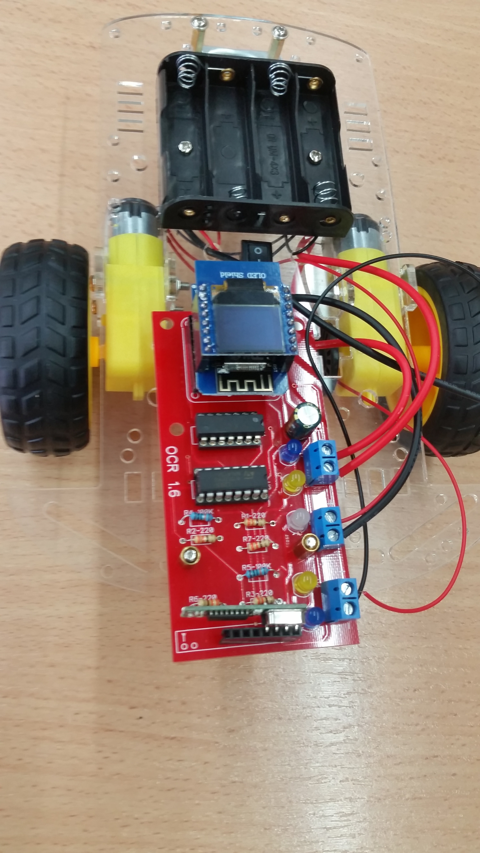
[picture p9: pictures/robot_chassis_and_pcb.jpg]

The completed robot.

## Test

   Turn on the robot. The robot should go forward about a meter and then back about a meter

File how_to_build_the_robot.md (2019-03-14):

1) Build the chassis:
   The chassis is the platform to which the rest of the parts are connected.
   Build the chassis according to the attached instructions.
   When done, you should have the two motors and the battery holder attached to the chassis.

The assembled robot chassis.
Note: the battery-holder wires should be routed to the top, and not as shown.

2) Solder the robot 'brain' and the associated display:
It is critical that all those parts are soldered exactly perpendicular.
    - the female 'socket' that connect the brain to the PCB
    - the male/female socket that is soldered to the brain
    - The 'male' pins that are soldered to the display.

The "brain" is the Wemos D1 Mini.

3) Build the electronic board. For this, you will need to solder the parts detailed at "Robot_hardware" to the supplied PCB.

The integrated circuits used:
- U1 is "Hex inverters" SN74LS04.
- U2 is "Bridge Power Driver" L239D
 
It is good to start with parts at the center, which are not high (because high parts make access to other parts hard).



The assembled PCB.

Note: The RF-receiver at the very bottom is optional.

4) Program the ESP8266 module
TBD

5) Connect everything together:
   Mount the PCB on the chassis. Connect the wires from the motors to the PCB. Connect the wires from the battery holder to the PCB.


The completed robot.

5) Test
   Turn on the robot. The robot should go forward about a meter and then back about a meter

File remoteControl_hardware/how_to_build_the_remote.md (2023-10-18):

The scematics of the remote control
===========================

Intrduciotion
-------------

The remote control is an optional part of the robots, that allows controlling the robot (move and turn) using the remote's buttons.
The remote transmits the commands on the free-use 433MHz radio frequency.

During the course, each student normally designs her own PCB (Printed Circute Board) for the remote. 
However, a pre-existing PCB design is present in this directory, if needed.
The software used for the schema capture and for the PCB design is the free version of diptrace. Sorrowfully, diptrace is available only under Windows. However, it is known to run under Linux/Wine.

The rest of the document intruduces the components used and the connections between them.

Terminal
--------
Connects the two wires from the battery holder to the PCB.
    Note: Mark the + and - so you will be able to tell where to connect the black/red wires.
    Note: The battery + is called Vcc. The battery - is called Ground.

Capacitor
---------
Connects to Vcc and to Ground. Stabilizes the voltage.
    Note: Mark the + on the PCB.

Microprocessor
--------------
Runs software that sends message to the robot using the RF module.
    Find by searching for component "PIC12F675_P":wq
    Sends a message when one of the keys are pressed.
    Microprocessor leg function list:
       - Leg number 1 connects to Vcc and leg number 8 to Ground.
       - Legs number 2, 3, 5 and 6 are connected to the switches; they are inputs.
       - Leg number 7 is connected to the RF module (pin 2) AND to the LED-resistor.      
       - Leg number 4 is not used.
    Note: Since the microprocessor needs to be available for software updates, it is not soldered directly to the PCB.
          Instead, a socket is soldered to the PCB and the microprocessor is inserted into the socket.
          This does not affect the PCB or the schematic.

LED and LED-resistor
--------------------
    The LED-resistor is connected to the microprocessor (leg 7) and to the + of the LED.
    The + of the LED is connected to the LED-resistor and the - to ground.
    Note: The resistor's function is to limit the current that passes through the LED.

RF module
---------
    The RF module sends information from the microprocessor to the robot as radio waves.
    RF module leg function list:
       - Leg number 3 connects to Vcc and leg number 4 to Ground.
       - Leg number 2 is connected to the microprocessor (leg 7).
       - Leg number 1 is not used.
    Note: you have to solder an antenna to the RF module. This does not affect the PCB.

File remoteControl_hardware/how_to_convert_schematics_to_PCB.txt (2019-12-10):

1) Load your schematics into the schematics editing tool
2) Do: "File" --> "Convert to PCB"
3) Click "OK" and "OK" to accept defaults
4) "View" --> "Units" --> "mm"
    "Route" --> "Layer Setup": select "Top" and change "Layer Type" to "Plane"
                --> "Route Setup" and set both "Trace width" and "Trace clearance" to 1
5) "Objects" --> "Create Board points" 
    Choose "Create rectangular board"
6) Place components:

7) Route

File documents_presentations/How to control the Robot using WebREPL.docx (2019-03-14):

How to control Ofek Robot using WebREPL:

You will need a computer with WiFi capabilities (wireless laptop, WiFi stick for PC, etc.)

1. Download WebREPL zip file from https://github.com/micropython/webrepl to a known folder on your computer.
2. Extract the files, and open webrepl.html.
3. Connect to the robot network: disable and re-enable computer network connection in order to see the robot. Connect to the robot from webrepl.html connect button.
4. Enter robot password: ofek
5. Now you can send instructions to the robot:
6. First, let’s call the robot r for simplicity: import robot as r
7. To control pulse width modulation: r.pwmLeft.value(1); r.pwmRight.value(1)
8. To control wheels move: r.dirLeft.value(1); r.dirRight.value(1)
9. Default value of the “value“ field is 0. Putting there 1 means changing robot’s direction.
10. Pressing up-arrow will show your last commands, you can use it to change values 0-1 instead of re-writing commands.

Now you can control your robot using this simple interface.

It is highly recommended, though, to search for more interesting automation ways:

- Take a deeper look in webrepl_cli.py (can be found in the downloaded WebREPL folder). It should help you upload batch files with full instruction set, instead of writing one command at a time.
- Search for Python WebSocket and see how you can control the robot using Python web interface.
- Do you think you are able to implement a TCP/IP server and adapt it to an Android application, so you can control the robot from your smartphone? What about web server that can handle instructions? Any other ideas?

Good luck

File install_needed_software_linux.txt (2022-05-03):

#This files explains how to install the Linux software needed to work with the ESP8266 'robot brain'

On Ubuntu:

- Install pillow: `sudo pip install pillow`
- Optional: install pinta: `sudo apt install pinta`

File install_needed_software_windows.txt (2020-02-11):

#This files explains how to install the Windows software that will enable you to work with the ESP8266 'robot brain'

The following software is needed for communicating with the robot over serial port
     (for example, when loading the intial firmware to the robot)
-----------------------------------------------------------------------------------
- Install python 3.x (x86-64, 64-bit) from python.org. 
     
      During the installation, enable the check-box "Add Python 3.7 to Path"

- Install the python modules needed to burn the robot-brain:
   `pip install adafruit-ampy`
   `pip install esptool pyserial`

- Install the serial driver for the 'Wemos D1 Mini' (AKA, the robot brain).

    Can be found in the file 'ch341ser_win_3.5.zip' 
    For example at https://wiki.wemos.cc/downloads

- Download and install the software 'putty'.
 
The following software is needed only to create new pictures:
-------------------------------------------------------------
- Install the 'pillow' Python modules:
     Open the command prompt (cmd) and issue the command:
     `pip install pillow`
- Optional: Install notepad++ (to edit code files) 
- Optional: Install paint.net (to edit the .bmp image files)

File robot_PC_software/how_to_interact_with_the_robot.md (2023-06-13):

# How to connect to the robot, using WiFi:

Connect the the WiFi network created by the robot. This network is normally called "Born"
  
Operations on the robot:

  - Connect to the robot "Python prompt": `./webrepl_cli.py -p ofek 192.168.4.1`
  - Get a file from the robot: `./webrepl_cli.py -p ofek 192.168.4.1:/app/script.
  - Send the file "script.py" to the robot: `./webrepl_cli.py -p ofek script.py 192.168.4.1:/another_name.py`

Note: The script `webrepl_cli.py` is from https://github.com/micropython/webrepl

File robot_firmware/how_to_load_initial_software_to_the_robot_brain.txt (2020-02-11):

Shalom Mitz			25TH March 2017

# OVERVIEW

The procedure below shows how to program the robot 'brain'.

The brain is the 'WEMOS D1 Mini' part, which is based on the ESP8266 processor.
The brain can be programmed with or without the display-module connected.

## Steps:

0) Make sure all needed software is installed on your PC, as detailed at the files "install_needed_software_linux.txt" and "install_needed_software_windows.txt"

1) Connect the robot-brain to a PC, using a normal 'Android' USB cable

2) Find the serial port used by the robot-brain:
   ON LINUX:
   Using terminal, run 'ls /dev/ttyUSB*'. This should show /dev/ttyUSB0
   If only /dev/ttyUSB2 exists, you should change 'burn' to reflect this
   If the 'ls' command above does not show anything, the D1 was not recognized.
   This must be resolved before continuing.

   ON WINDOWS:
      Normally, "COM4" is used on Windows
      To see the actual port:
         - Open the "Device Manager":
             - Right-click on "Computer" or "This PC" icon
             - At the menu that will open, choose "Manage"
             - choose "Device Manager"
         - Expand "LPT and COM ports"
         - Notice the existing serial ports (called "COM" and a digit)
         - Plug-in the robot brain to the PC, using a USB cable
         - Notice the name of the new COM port. This is normally "COM4"

Note: 
   Normally we program the brain with the firmware-image file present in this directory.
   However, you can also use the generic microPython image, present at http://micropython.org/download#esp8266

3) Program the brain with the microPython image: 
   ON LINUX: Simply run './burn'
       Note: 'burn' depends on the 'serial' Python module.
   ON WINDOWS:
       - Open command prompt (Run: cmd)
       - `esptool.py erase_flash`
       - Change to directory containing the file firmware.bin
       - `esptool.py write_flash 0 firmware.bin`

4) Sanity check: disconnect the D1 from the USB and plug back.
   When you re-connect the D1, one of the LEDs should blink twice.
   If the LED does not blink, or blink all the time, try to run 'burn' again
   Note: Detailed instructions of programming the D1 and troubleshooting can be found at:
   http://docs.micropython.org/en/latest/esp8266/esp8266/tutorial/intro.html#deploying-the-firmware

5) Burn the additional files:
   Run:
     - On Windows: 'send_all_files_windows'
     - On Linux:   './send_all_files_linux'

Testing:

   - Once you get the ">>>" prompt:
     enter the command "import 

1) Connect to the brain: 
   Once connected, the brain looks like serial port at /dev/ttyUSB0 (rarely: /dev/ttyUSB1) on Linux or CAM4 on Windows.

   You can connect to it using: putty, minicom, screen, or any other 'terminal emulation' software
   Here are detailed instructions using Putty:

   - Open putty
   - Define a serial session: 
      - Choose "Serial" as the connection type     
      - Set the port (Normally: COM4 or /dev/ttyUSB0)
      - Set the speed: 115200
   - Open the connection: Click on "Open"
   - Press "Enter": you should see the Python prompt (>>>)
     Do not continue to the next steps before you get the prompt !
     You can try to close Putty, disconnect the brain, reconnect the brain and launch putty again.
     You can also try to burn the image again.

   Once you are connected, hit "Enter" few times, and you should get the ">>>" REPL prompt.
   If you do not get the prompt, try unplugin/plugin from USB. If this fails, try 'burn' again.
   There is no point to continue w/o the REPL prompt.

   Also, once you are connected, you can type the command "import demo".
   This should send few strings to the console and then display some pictures on the attached display. 

Steps that are repeated each time the D1 is used:
1) Connect to the PC/laptop to the WiFi access-point created by the D1:
   Look at the available WiFi networks for a network called "MicroPython-xxxxxx" (the 'xxxxxx' part is different for each D1)
   Connect to this network.
   Note: This will probably disconnect you from the Internet. 

2) Connect to the robot using WebREPL:
   If needed, download the webrepl files from  https://github.com/micropython/webrepl.
   Open the file "open webrepl.html in a browser. 
   You should get a prompt to choose password (first time) or login.
   After login, you should get the ">>>" prompt. You are also able to upload and download files.
   There are more details at: https://github.com/micropython/webrepl

3)    Using WebREPL, import the 'robot' module. This will define 4 outputs:
    pwmRight, dirRight, pwmLeft, dirLeft
    Each of those can be set to high or low, for example:
    pwmRight.low() or pwmLeft.high()

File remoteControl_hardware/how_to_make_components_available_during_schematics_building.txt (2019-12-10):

1) Open the "Schematic capture" software from the "DipTrace launcher"
2) From the top-menu, select "Library" and then "Library Setup"
3) Now at the "Library Setup" window: 
      At "Groups", choose "User Components"
      Click "Add Library" and add "remoteControl_diptrace_components"  (At Ofek, this is at "W:\remote_control")
      click "OK" to close the "Library Setup" window.
4) At the upper/left corner of the main window, click on "Project Libraries" and choose "User components"
    Just below, click on "remoteControl_components"

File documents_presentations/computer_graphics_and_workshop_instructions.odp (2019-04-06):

## Computer Graphics

Introduction & Workshop information

Shalom Mitz

shalommmitz@gmail.com

Ofek School for Gifted Childrens

April 2019

## Our context:

- Free software
- Open Source
- github

## Introduction to computer graphics

- Image is composed of Pixels
- Pixels are the "dots" in the image
- Cordinate: which line and coloumn

## The robot display

- :
- Two colors only
- 48 lines by 64 columnes

## What we need to do

  Create images for common situations:
- - Booting
- - Testing motors
- - Waiting for the remote
- - Remote found, accepting commands
- - Awaiting Python command
- - WiFi client connected
- Create fun images
- Create showcase animations

## How to create and test an image

  Overview:
- create -> preview -> optionaly: improve -> export to .hexImage -> upload to robot -> use
- Details: ....

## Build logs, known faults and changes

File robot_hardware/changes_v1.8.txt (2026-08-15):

1. New PCB-to-wire part: 4 legs, w/o screws
2. Added sw-controlled LED
3. Add a LED to indicate reception of RF signal.
4. Moved from ESP8266 to ESP-32 S2

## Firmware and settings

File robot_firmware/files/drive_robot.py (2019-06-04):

from machine import Pin as pin, PWM
import utime,  os

OFF = 0; ON = 1 
LED_OFF = 1; LED_ON = 0 
FORWARD = 1; BACK = 0
pwmRight = pin(14,pin.OUT)
dirRight = pin(15,pin.OUT)
pwmLeft = pin(12,pin.OUT)
dirLeft = pin(0,pin.OUT)
LED = pin(2,pin.OUT)
LED.value(LED_OFF)



def move(dir):
    if dir=="l":
        dirRight.value(FORWARD); dirLeft.value(BACK); duration = 0.55
    elif dir=="r":
        dirRight.value(BACK); dirLeft.value(FORWARD); duration = 0.55
    elif dir=="b":
        dirRight.value(BACK); dirLeft.value(BACK); duration = 1
    else:
        dirRight.value(FORWARD); dirLeft.value(FORWARD); duration = 1
		
    pwmRight.value(ON);  pwmLeft.value(ON);  utime.sleep(duration)
    pwmRight.value(OFF); pwmLeft.value(OFF); utime.sleep(0.1)
	
print("Blinking LED")
for i in range(4):
    LED.value(LED_ON); utime.sleep(0.3)
    LED.value(LED_OFF); utime.sleep(0.5)    

while True:
    dir = input("Enter l for Left, r for Right, b for back, f for forward > ")
    move(dir)

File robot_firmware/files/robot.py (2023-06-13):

from machine import Pin as pin, PWM
import utime, rf, os, ubinascii
import display

OFF = 0; ON = 1 
LED_OFF = 1; LED_ON = 0 
FORWARD = 1; BACK = 0
pwmRight = pin(14,pin.OUT)
dirRight = pin(15,pin.OUT)
pwmLeft = pin(12,pin.OUT)
dirLeft = pin(0,pin.OUT)
LED = pin(2,pin.OUT)
LED.value(LED_OFF)

def setRobotId(id):
    f = open("robot_id", 'w')
    f.write(str(id) + chr(10))
    f.close()

def executePacket(msgDict):
    print ("Executing:")
    for k in msgDict.keys():
        print("   ", k, msgDict[k])
    if msgDict["rightMotorDirction"] == "FORWARD":
        dirRight.value(FORWARD)
    else:
        dirRight.value(BACK)
    if msgDict["leftMotorDirction"] == "FORWARD":
        dirLeft.value(FORWARD)
    else:
        dirLeft.value(BACK)
    pwmRight.value(ON);  pwmLeft.value(ON)
    print("Motors will be on for", msgDict["rightMotorDuration"]/100)
    #utime.sleep(msgDict["rightMotorDuration"]/100)
    utime.sleep(0.34)
    pwmRight.value(OFF); pwmLeft.value(OFF)

# Step 0: Init display and say hello :)
d = display.Display()
d.clear()
d.text(0,0,"Hi :-)")


# Step 1: get and blink robot ID
ROBOT_ID = 2
if 'robot_id' in os.listdir():
    f = open("robot_id")
    robot_id_str = f.read()
    robot_id_str = robot_id_str.replace(chr(10), "").strip()
    ROBOT_ID = int( robot_id_str )
    f.close()

print("Robot id is", ROBOT_ID)
d.text(0,12, "ID is "+str(ROBOT_ID))
utime.sleep(1)
for i in range(ROBOT_ID):
    LED.value(LED_ON); utime.sleep(1)
    LED.value(LED_OFF); utime.sleep(1)    

# Step 2: Test motors
print("Step 2: Test motors")
d.text(0,36, "Forward")
dirRight.value(FORWARD); dirLeft.value(FORWARD)
pwmRight.value(ON);  pwmLeft.value(ON);  utime.sleep(3)
pwmRight.value(OFF); pwmLeft.value(OFF); utime.sleep(1)
d.text(0,36, "Back   ")
dirRight.value(BACK); dirLeft.value(BACK)
pwmRight.value(ON);  pwmLeft.value(ON);  utime.sleep(3)
pwmRight.value(OFF); pwmLeft.value(OFF); utime.sleep(1)
LED.value(LED_OFF)
d.clear()
d.text(0,12, "ID is "+str(ROBOT_ID))

# Step 3: Enter rf-recption mode, if received valid command before time-out
print("Step 3: Enter rf-recption mode")
d.text(0,36, "Wait for")
d.text(0,48, "   RF")
# Step 3.1: make led blink: 
#           50% duty cycle, 4 Hz. Led is 0.125 sec on and 0.125 sec off
pwm = PWM(LED, freq=4, duty=512) 
utime.sleep(1)
pwm.deinit(); LED.value(LED_ON)
# Step 3.2: Wait for 10 seconds for valid command
r = rf.RF()
end_time =  utime.time() + 10
packet = None
while (utime.time()<end_time) and not packet:
    packet = r.getPacket()
    print("Got packet of len", len(packet))
    if len(packet)==0: packet = False
# Step 3.3: Switch off the LED and deinitialize/stop the timer
LED.value(LED_OFF)
# Step 3.4: Valid packet received - wait for more packets until reset 
if packet:
    d.clear()
    d.text(0,12, "ID is "+str(ROBOT_ID))
    d.text(0,36, "RF mode  ")
    while True:
        if packet: 
            print( "Got RF packet:"+ str(ubinascii.hexlify(packet)) )
            msgDict = r.interpetMsg( packet)
            print( "packet fields:"+ str(msgDict) )
            if "Error" in msgDict.keys():
                print("Ignoring rf packet because it is not well formed")
            elif str(msgDict["remoteId"]) != str(ROBOT_ID):
                print("Ignoring rf packet: wrong robot ID. Expected:"+ str(ROBOT_ID) +" Got from rf:"+ str(msgDict["remoteId"]) )
            else:
                executePacket(msgDict)
        packet = r.getPacket()

# Step 3.5: No valid packet received - will exit
d.clear()
d.text(0,12, "ID is "+str(ROBOT_ID))
d.text(0,36, "Repl mode")
print("Done")

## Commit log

2019-03-14 Added pic of assembled chassis.
2019-03-25 Added files and procedure to burn the robot brain
    [demo.py, display.py, rf.py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]
2019-05-22 added remote-control PCB and schematics files
    [BoardOutline.gbr, BottomMask.gbr, BottomPaste.gbr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]
2019-05-28 Now rejects rf packets (from remote) of wrong robot-id.
    [rf.py, robot.py]
2019-12-03 Added pattren for big push-button
2022-05-23 Minor fixes to the robot_firmware files
    [robot.py, verifyFiles.py]
2022-05-24 Remote-control firmware: added firmware that WORKs w/current robot sw (RC_RF629.pbp) The file RC_RF629_multiKey_do_not_use.pbp support multi-key pressed at the same command, but is NOT compitable w/c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
2022-09-02 remote control: fixed size of push button holes + moves outline of rf transmitter
2022-09-02 robot PCB design: bumbed version to 1.7 + enlarged screw-terminal holes + improved power supply traces
2022-09-02 robot schematic: added IC part numbers table + bumped version to 1.7
2022-09-03 robot PCB v1.7: fixed legend on PCB + generated Gerber files for manfacturing
2022-09-05 Added spreadsheet with parts+prices+purchase URLs
    [22_08_Ofek_robotics_purchases.ods]
2022-09-06 Enhanced a few documents
    [22_08_Ofek_robotics_purchases.ods, 22_08_Ofek_robotics_purchases.xlsx]
2023-06-13 robot.py: fixed a bug: if no remote-controller packet is returned, it used to crash on empty packet.
    [robot.py]
2023-06-13 Added reporting of current stage in the display
2023-10-18 Minor: doc corrections
    [BoardOutline.gbr, BottomMask.gbr, BottomPaste.gbr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]
